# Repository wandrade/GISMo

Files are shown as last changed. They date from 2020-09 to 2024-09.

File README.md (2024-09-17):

# G.I.S.Mo

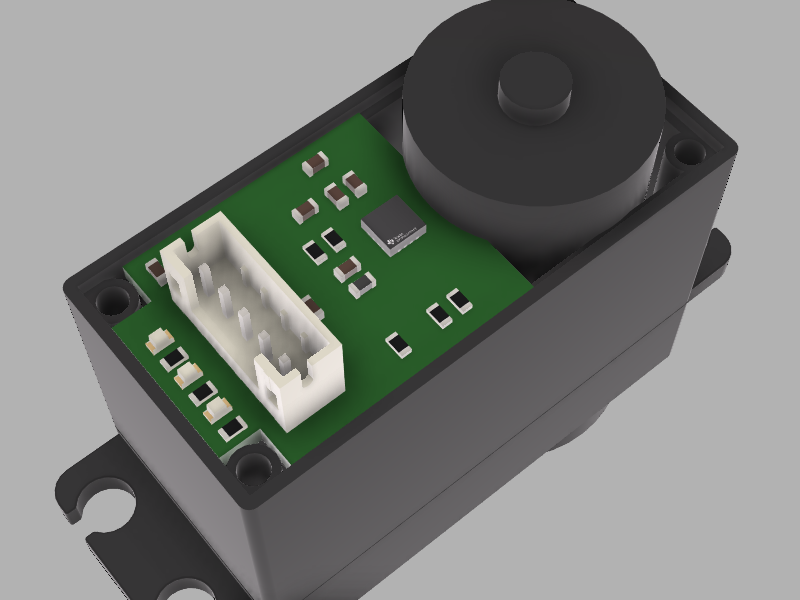
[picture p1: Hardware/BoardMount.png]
Board Mount
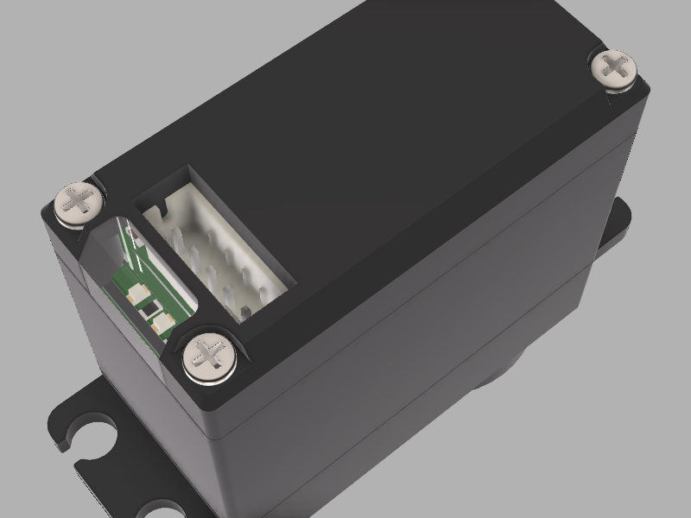
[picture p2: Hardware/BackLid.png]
G.I.S.Mo Board
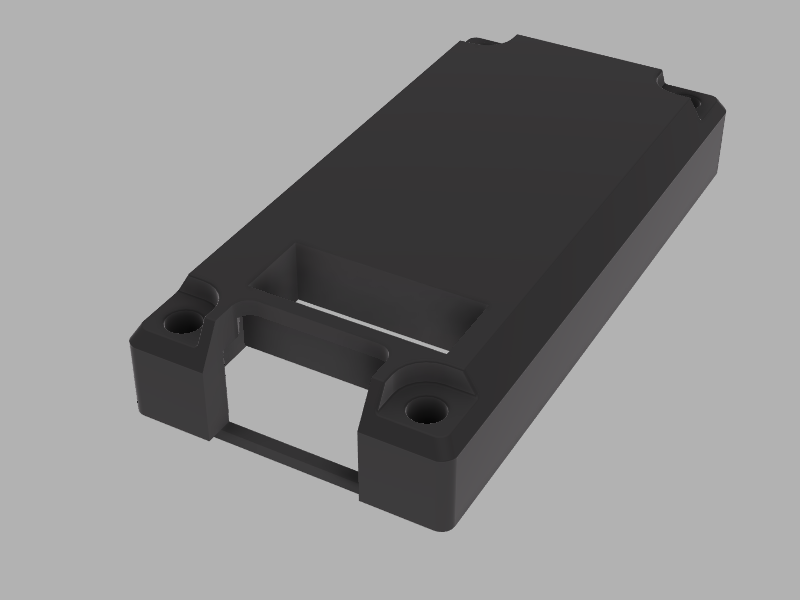
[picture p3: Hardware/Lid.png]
Lid
  |   | 
:-------------------------:|:-------------------------:|:-------------------------:

After a long search, I have failed to find a servo motor that does everything I need for my projects that is also cheap(ish) and fully programmable (say no to closed source stuff whenever you can).

Well, thus was born the idea of GISMo (Greatly Inteligent Servo Motor). This project aims to develop a board that can be used to replace the vanilla servo driver boards that comes with cheaper ones such as MG995 and MG996R, giving it more power and making it more usefull for distributed controll projects:

Wishlist:
- [x] Embedded MCU (STM32F302 powered!) 
- [x] Current sensing (for torque controll and power management features) 
- [ ] I2C interface (or if you please, just change a bit the circuit to use whatever interface you want)
- [x] Programable LED's (because they are cool)
- [x] Absolute magnetic encoder (at least 12bits)
- [x] Free range of movement (180 degrees is just not enough)
- [ ] Control:
    - [ ] Simple position PID loop
    - [ ] MISO controller for speed and position simultaniously (Probably a state space controller)
    - [ ] Torque controll loop
    - [ ] Trapezoidal position curve following
- [ ] Configurable parameters
    - [ ] Speed/Position/Current limit
    - [ ] Controller mode
    - [ ] Configurable break zone (turn on break when position reaches its demand and settles)
    - [ ] Multiturn counter
    - [ ] Controller gains (PID and state space gain matrix)
- [ ] ROS2 Interface node:
    - [ ] Hot plug I2C device detection
    - [ ] Configuration via YAML and ROS Param
    - [ ] up to 16 Individually addressed servos

# Organization
The project contains 3 main blocks: first is the hardware, using [KiCad](https://kicad-pcb.org/), in the Hardware folder you will find 2 subfolders, one for the dev board, which is a big version of the board with some more stuff to facilitate firmware development and debugging, and a second one that contains the GISMo board that actually fits in the servo (to be made).
Then we have the Firmware with two other bits, the [CubeMX](https://www.st.com/en/development-tools/stm32cubemx.html) project so we have everything neatly initialized in our MCU, and the actual firmware and its libs.

# Version History
Now this is a bit tricky. I have 3 things to version and no interest in havving 3 different repos for them at all, so ill trake and make it sensible.

Each sub-thing will have its own sub-version, and once I have a combination of the 3 of them that kind of works, I will merge it into the master branch and tag it with a overall version of the repo (if that makes sense).

## Firmware
--

## GISMo Board
- [Interactive BOM](http://htmlpreview.github.io/?https://github.com/wandrade/GISMo/blob/develop/Hardware/GISMoBoard/bom/ibom.html)

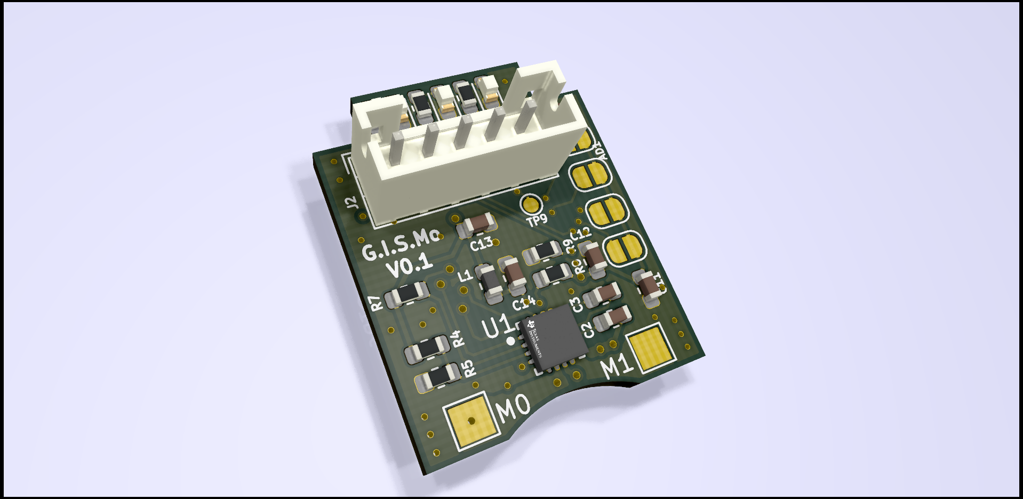
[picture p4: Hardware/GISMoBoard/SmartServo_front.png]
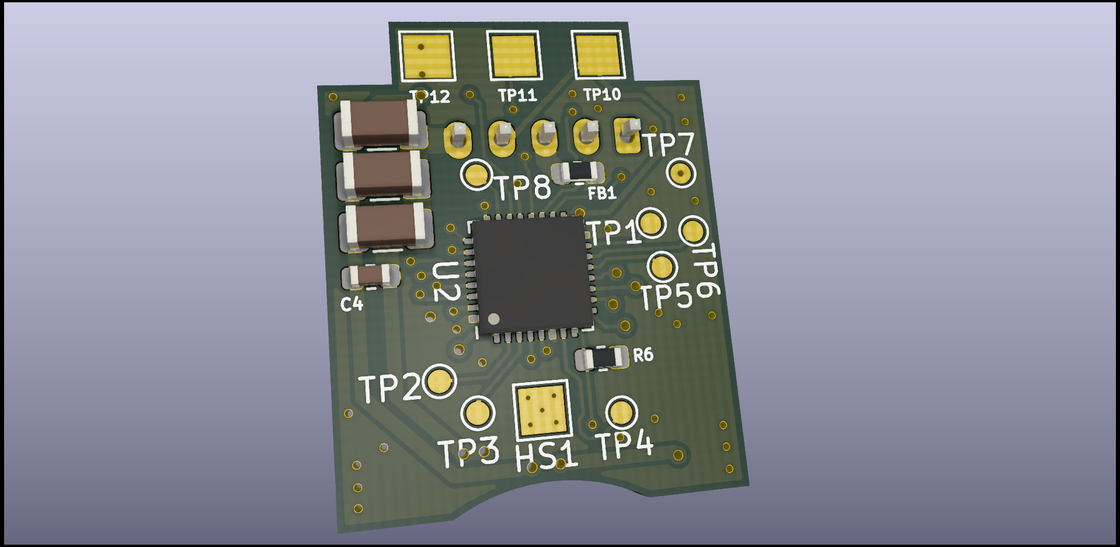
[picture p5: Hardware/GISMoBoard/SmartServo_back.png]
 | 
:-------------------------:|:-------------------------:
- 0.0.1 - Copy of dev board with a few changes to reduce space usage
    - Only one I2C/Power plug
    - Replaced Address header pins by solder jumpers
    - Motor and PWM sensor connectors replaced with solder pads
    - Included a heat sink pad under the motor driver
    - Removed Crystal and oscilator
    - Reduced LED packages
    - Removed Debug connector
    - Removed reset button

## Development Board
- [Interactive BOM](http://htmlpreview.github.io/?https://github.com/wandrade/GISMo/blob/develop/Hardware/DevBoard/bom/ibom.html)

This board is meant for circuit testing and ease of debugging.
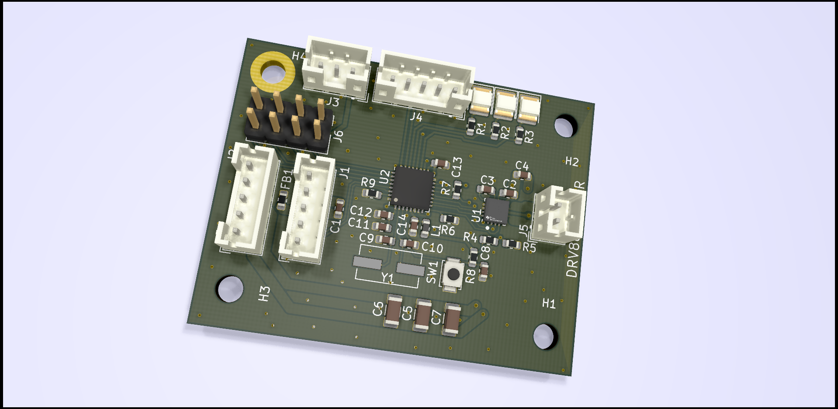
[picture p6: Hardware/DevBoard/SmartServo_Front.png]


- 0.0.1 - Initial proposal board for development board schematic and layout.
    - [STM32F302K8 MCU](https://www.st.com/en/microcontrollers-microprocessors/stm32f302k8.html) - Small package and seemingly enough processing power for everything we need.
    - [DRV8876RGTR Driver](https://www.ti.com/store/ti/en/p/product/?p=DRV8876RGTR) - Has more than double the current needed and provides an inbuilt current sensing solution (hopefully good enough)

# Costs
Here I will keep track of how much you have to pay for each of the more expensive bits so you have an idea of how much a working GISMo will cost you.

# FAQ
I have barely started this project and everytime I tell somebody about it, I get the same questions, so here we go:

- Why not use a normal DC motor with drivers tailored for each project:
    - Cause I like modular! It saves time and you dont have to do everything multiple times. Plus, a lot of the stuf you find online if you are 3D printing, is already made for this size motor. Plus Plus, sorting out motor specifications, gearboxes, making gears (when necessary) is all just a pain, this one can do a lot of the stuff I need for anyway (robotic arms and legged robots).

- Why not just buy a smart servo? this one will probably cost almost the same as the comercial ones.
    - For one, i Hope to make it at least the same price as the "cheap" smart servos. But really, mainly, so I can have full power over its features and its firmware. Also cause its fun!

For now that is it, lets see what comes next :)

# License
Everything under this repository is free to use unless it is used to generate profit. The license states that it CAN be used for comercial puproses, however an agreement have to be reached between the original creator of this project (Werner Thomassen Andrade) and the interested parties before that can happens.

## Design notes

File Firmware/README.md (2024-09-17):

# G.I.S.Mo Firmware

This section of the repo is all about the firmware powering the board. Architecture, implementation decisions, methods and so on.

# Overall Structure
The firmware has a few main components:
- PWM position encoder reading
- Motor current reading
- Control algorithms
- Communications and interface

Each one will be detailed as they are developed
## Softwares and tools
CubeMX
CubeMonitor
CubeIDE

## I²C interface
To learn more about it and how to implemente it go to these articles:
* https://deepbluembedded.com/stm32-i2c-tutorial-hal-examples-slave-dma/
* https://visualgdb.com/tutorials/arm/stm32/i2c/

and have a look. It is very easy and well explained, starting from the theory then jumpping into the implementation used by STM32 MCUs

## PWM Encoder
### Choosing an encoder
This projects aims to use either the magnetic encoder [AS5600](https://www.mouser.co.uk/datasheet/2/588/AS5600_DS000365_5-00-1877365.pdf) or [AS5048x](https://ams.com/documents/20143/36005/AS5048_DS000298_4-00.pdf/910aef1f-6cd3-cbda-9d09-41f152104832). They both have the same PWM interface so it should be just a matter of choosing your preference and it will work.

They are part of a [family of magnetic absolute encoders](https://ams.com/angle-position-on-axis) that can read the orientation of a magnet with respect to the chip with high precision and speed.
The chips are robust to external magnetic fields, temperature changes and slight mechanical variations such as eccentricity and distance from the chip, making it a very robust and easy to use option. The downside? Cost, mor on that soon.

So I reckon that 12bits (that is down to 0.08789 degrees)it more than enough in terms of precision for a smart servo and the purposes that we are aiming for here, there are cheaper versions of such encoders that have a smaller precision such as 10bits but that is just not enough. of course if 14 and 16 and 22 bit would be awesome... but not so much when we have every intention of making at least 12 of these motors to build a nice robot spider.  So on that range there are a few choices as you can see in the links above, but two of them caught my attention and here is why:

- AS5600 - One of the cheapest ones, goes for around £2.50 a pop. downside is that you have to pre-configure the PWM output to run at a high frequency, and it only get to 920Hz.
- AS5048x - 3 Times the price of the above, but its slightly faster (1Khz) and come ready t go, you just solder it to the PCB and plug it in.

Arguably that is not fast enough for a position encoder, especially since we are deriving the speed out of it too. But for most applications that should be enough. If not then hey! this is open source! feel free to slightly change the pins you expose for the sensor and you can use something faster or with better precision such as the AS5048 SSI interface or any other encoder that suits you really.

### Reading it
While explaining how i have implemented the sensor reading, I assume you have the code open on the other half of the screen so you can actually know what im talking about.

Now on the datasheet there is a nice diagram of the PWM signal that you can expect out of the chip (just click on the link of the previous section of any of the encoders and search for 'PWM' you will find it in no time).

For reading a PWM without risking to loose any valuable readings due to bad implementation (and after much trial and error), I have found that the best way is to get a timer on the pin that has both direct and indirect capture on separate channels (Just open the CubeMX project and look at how timer 1 is configured).

This will allow me to start 2 interrupts on the same pin, one for the rising edge of the PWM and another for the falling edge.
As stated in the datasheet, the signal is not 100% information, you have in total 4119 clocks on each cycle, 12 are always high as a 'init' bit set, then there are 4 reserved for errors, then the next 4095 are the actual data and finally some more 8 clocks that are always low, as e 'exit' bit set.

The full duty cycle can vary a little bit, so its better to also read the period of each one to use in the calculations so we have a more precise measure. Right to continuing...

You set an interrupt at the falling edge (after the duty cycle is completed) but you don't need to set up a callback function for it. All we need to know is when that edge ocurred, and we don't need to waste CPU time putting that into a variable, since the chip already does that for us, we just have to access it like 'htim1.Instance.CCR#' where # is the number of the channel that got interrupted.

On the rising edge tho, we want to have a callback, but it has to be really fast (otherwise we wont have enough CPU for al the rest), in order to spent less CPU time on bullshit, I have disabled the code generation for timer1 (On cubeMX System Core->NVIC->Tim1 capture compare interrupt) because the HAL implementation of it that all tutorials tell you to use do LOADS of ifs and elses to check what sort of interrupt that is and that is just a waste of time, since we know what timer 1 is being used for. After disabling the code generation, all we have to do is define the 'void TIM1_CC_IRQHandler(void)' function on the main and that is our callback, simple as that. (look at the code for the other stuff you have to do in there).

Now that the callback is handled, what we need to do to fully read our position goes as follow (and you can see the full implementation just by following everything in void TIM1_CC_IRQHandler(void) on main.c):

- Reset timer - We want the timer count to start at the beginning of the cycle, and then finish at the end of it (obviously) and that will be your full period time.
- Save CCR3 and CCR4 (interupt times of rising and falling edges) ASAP - They get overwritten when another interrupt comes in, so we want to save that into another variable to be able to use it reliably all the way trough.
- Transform the timer count of our CPU (which is running at 64Mhz, so around 64K counts per period) to the clock timing of the sensor, which is 4119 per cycle.
- Process the data
    - Some error checking is always good (if there is not enough clock times that means that there is an error on the sensor, if there is too much it means there is no sensor at all).
    - Calculate the position of the encoder
    - (Optional) Count the number of turns that happened for multiturn applications.
    - Put both single turn position and multiturn count in one variable. why?
        - After the callback finishes, we need to read those values on lower priority threads to actually use it, so you want to be sure that you have read the whole thing before starting to process. If you have to read two variables, you might get interrupted after reading the first one, then another measures come in and then you read the second one of a different reading, so you get inconsistent data.
        - If you put them together like i did there, you have just one number that tells you the absolute position including multiturn, it just works nicely, and you only have to scale the thing once to transform from raw to readable angle.
- That is it!

The thread that does this will have the highest priority of the bunch for reasons that will be explained in the section appropriate for that. (You can set this priority on CubeMx under System Core->NVIC->Tim1 capture compare interrupt).

Maybe i'll put some diagrams and pictures here in the future to make this easier to understand, who knows?!

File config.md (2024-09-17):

sudo tar xjf gcc-arm-none-eabi-YOUR-VERSION.bz2 -C /usr/share/

sudo ln -s /usr/share/gcc-arm-none-eabi-YOUR-VERSION/bin/arm-none-eabi-gcc /usr/local/bin/arm-none-eabi-gcc 
sudo ln -s /usr/share/gcc-arm-none-eabi-YOUR-VERSION/bin/arm-none-eabi-g++ /usr/local/bin/arm-none-eabi-g++
sudo ln -s /usr/share/gcc-arm-none-eabi-YOUR-VERSION/bin/arm-none-eabi-gdb /usr/local/bin/arm-none-eabi-gdb
sudo ln -s /usr/share/gcc-arm-none-eabi-YOUR-VERSION/bin/arm-none-eabi-size /usr/local/bin/arm-none-eabi-size
sudo ln -s /usr/share/gcc-arm-none-eabi-YOUR-VERSION/bin/arm-none-eabi-objcopy /usr/local/bin/arm-none-eabi-objcopy

sudo apt install libncurses-dev
sudo ln -s /usr/lib/x86_64-linux-gnu/libncurses.so.6 /usr/lib/x86_64-linux-gnu/libncurses.so.5
sudo ln -s /usr/lib/x86_64-linux-gnu/libtinfo.so.6 /usr/lib/x86_64-linux-gnu/libtinfo.so.5

install USBIP Connect vscode extention in wsl
install the client on windows host
(follow instructions on extention page)

sudo apt install openocd

install extension VsCode Action Buttons

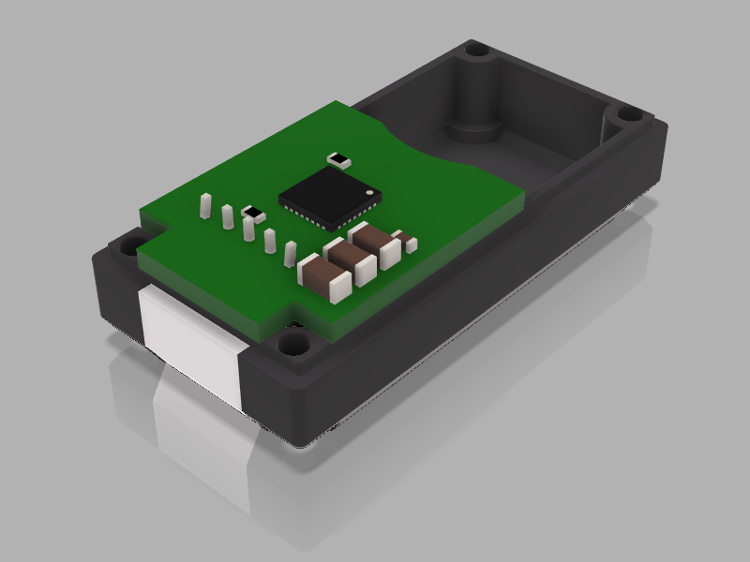
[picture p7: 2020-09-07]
Hardware/Lid_with_PCB.png

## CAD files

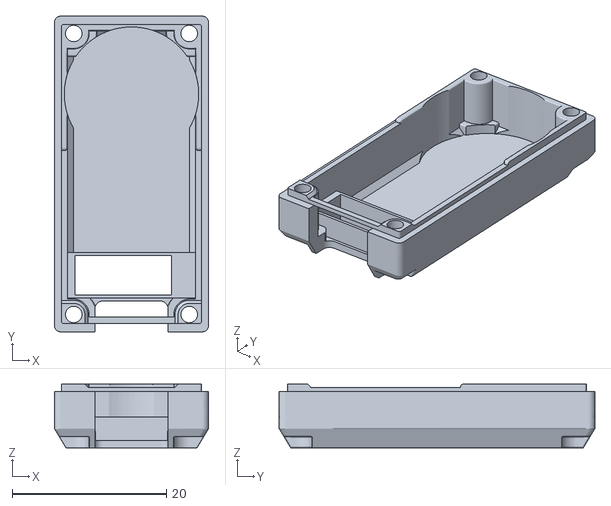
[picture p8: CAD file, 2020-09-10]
Hardware/BackLid.stl
20.0 x 41.0 x 8.30

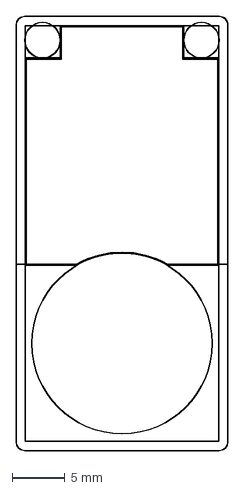
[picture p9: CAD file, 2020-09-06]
Hardware/GISMoBoard/BoardOutline.dxf
20.0 x 41.0 mm

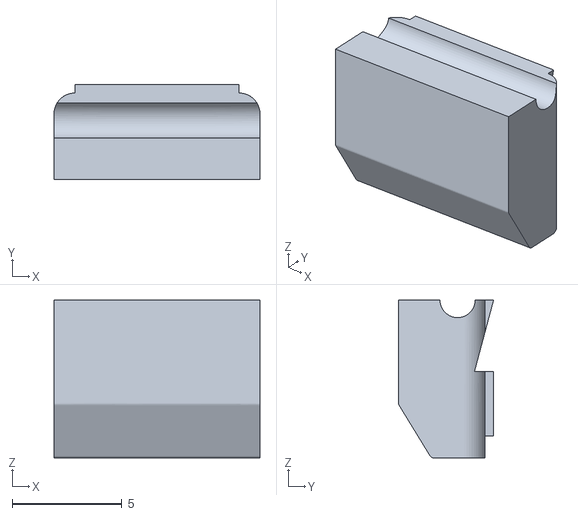
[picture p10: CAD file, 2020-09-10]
Hardware/LED_Screen.stl
9.40 x 4.34 x 7.20

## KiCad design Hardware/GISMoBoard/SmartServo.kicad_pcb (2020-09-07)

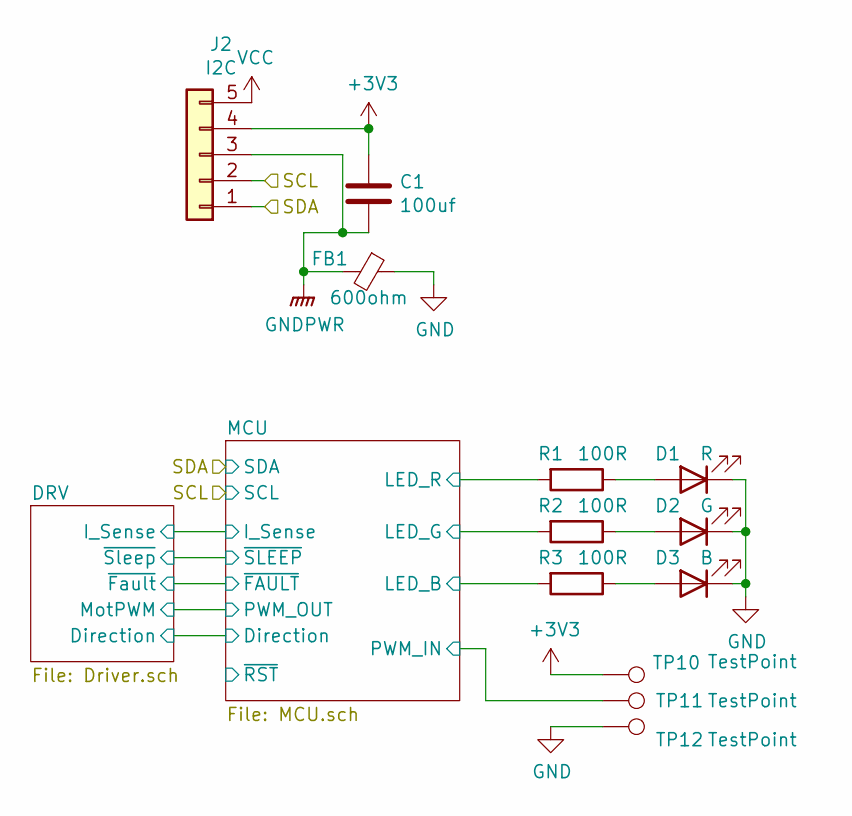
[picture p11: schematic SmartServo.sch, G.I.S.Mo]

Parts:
C1: 100uf; C_0603_1608Metric
D1: R; LED_0603_1608Metric
D2: G; LED_0603_1608Metric
D3: B; LED_0603_1608Metric
FB1: 600ohm; R_0603_1608Metric
J2: I2C; JST_PH_B5B-PH-K_1x05_P2.00mm_Vertical
R1, R2, R3: 100R; R_0603_1608Metric
TP10, TP11, TP12: TestPoint; TestPoint_Pad_2.0x2.0mm

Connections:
+3V3: C1.1, J2.4, TP10.1; also elsewhere on the board
/MCU/LED_B: R3.2; also elsewhere on the board
/MCU/LED_G: R2.2; also elsewhere on the board
/MCU/LED_R: R1.2; also elsewhere on the board
/MCU/PWM_IN: TP11.1; also elsewhere on the board
/SCL: J2.2; also elsewhere on the board
/SDA: J2.1; also elsewhere on the board
GND: D1.1 (K), D2.1 (K), D3.1 (K), FB1.1, TP12.1; also elsewhere on the board
GNDPWR: C1.2, FB1.2, J2.3; also elsewhere on the board
unnamed: D1.2 (A), R1.1
unnamed: D2.2 (A), R2.1
unnamed: D3.2 (A), R3.1
VCC: J2.5; also elsewhere on the board

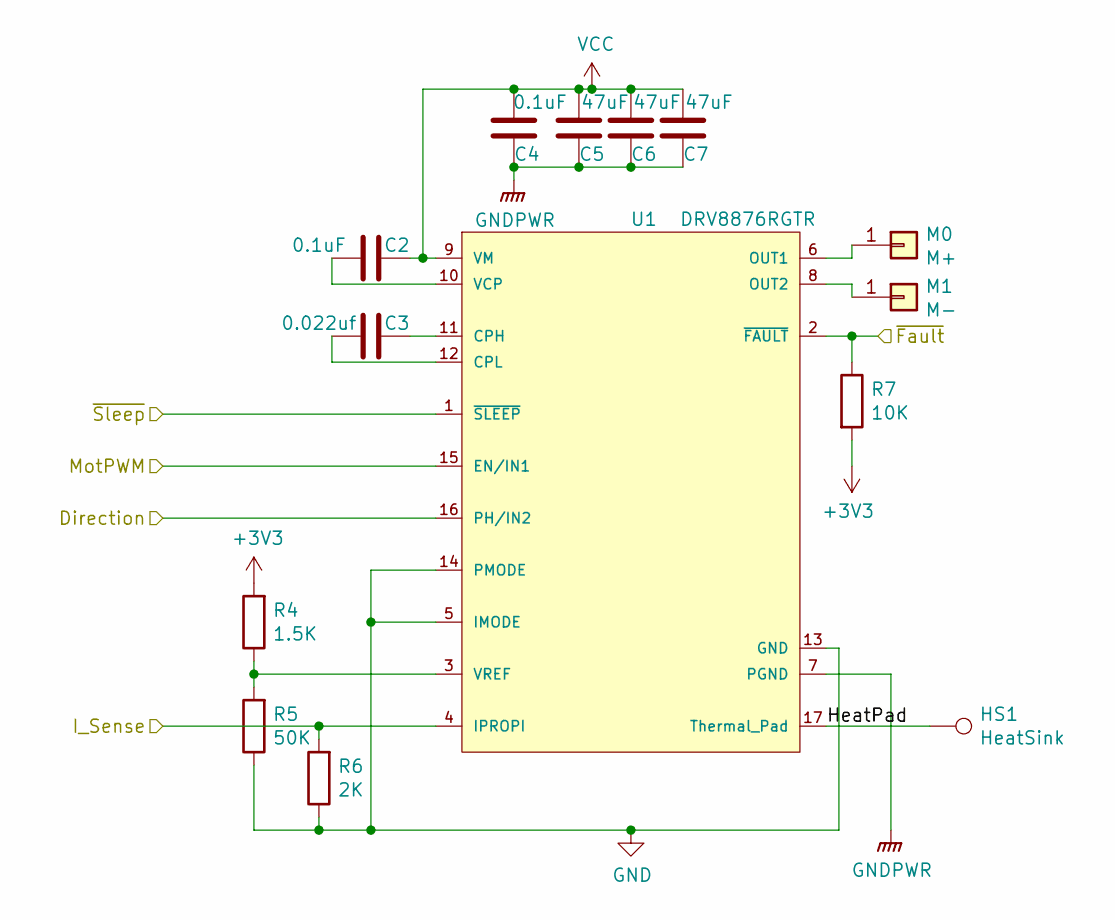
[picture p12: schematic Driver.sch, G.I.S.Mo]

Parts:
C2, C4: 0.1uF; C_0603_1608Metric
C3: 0.022uf; C_0603_1608Metric
C5, C6, C7: 47uF; C_1206_3216Metric; Farnell https://uk.farnell.com/tdk/c3216x5r1e47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
HS1: HeatSink; TestPoint_Pad_2.0x2.0mm
M0: M+; TestPoint_Pad_2.0x2.0mm
M1: M-; TestPoint_Pad_2.0x2.0mm
R4: 1.5K; R_0603_1608Metric
R5: 50K; R_0603_1608Metric
R6: 2K; R_0603_1608Metric
R7: 10K; R_0603_1608Metric
U1: DRV8876RGTR; Texas_Instruments-RGT0016C-0-0-MFG; mouser part number 595-DRV8876RGTR

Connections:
+3V3: R4.2, R7.2; also elsewhere on the board
/DRV/Direction: U1.16 (PH/IN2); also elsewhere on the board
/DRV/HeatPad: HS1.1, U1.17 (Thermal_Pad)
/DRV/I_Sense: R6.2, U1.4 (IPROPI); also elsewhere on the board
/DRV/MotPWM: U1.15 (EN/IN1); also elsewhere on the board
/MCU/~FAULT: R7.1, U1.2 (~FAULT~); also elsewhere on the board
/MCU/~SLEEP: U1.1 (~SLEEP~); also elsewhere on the board
GND: R5.1, R6.1, U1.5 (IMODE), U1.13 (GND), U1.14 (PMODE); also elsewhere on the board
GNDPWR: C4.1, C5.1, C6.1, C7.1, U1.7 (PGND); also elsewhere on the board
unnamed: C2.2, U1.10 (VCP)
unnamed: C3.1, U1.11 (CPH)
unnamed: C3.2, U1.12 (CPL)
unnamed: M0.1, U1.6 (OUT1)
unnamed: M1.1, U1.8 (OUT2)
unnamed: R4.1, R5.2, U1.3 (VREF)
VCC: C2.1, C4.2, C5.2, C6.2, C7.2, U1.9 (VM); also elsewhere on the board

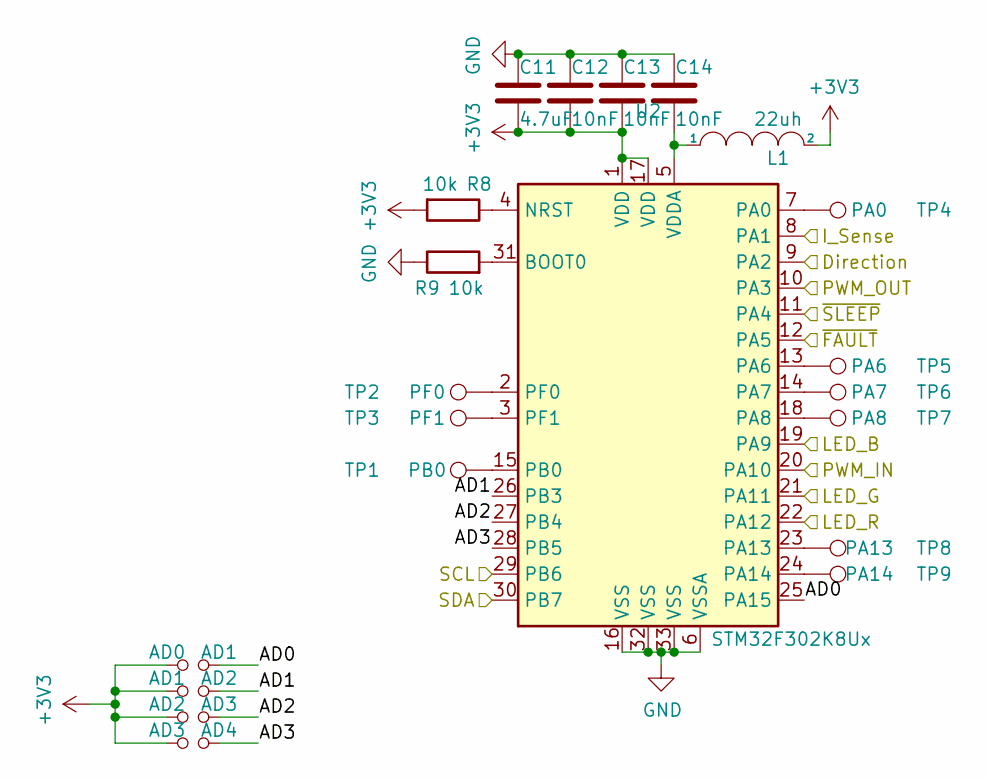
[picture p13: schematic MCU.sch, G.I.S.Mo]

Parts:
AD1: AD0; SolderJumper-2_P1.3mm_Open_RoundedPad1.0x1.5mm
AD2: AD1; SolderJumper-2_P1.3mm_Open_RoundedPad1.0x1.5mm
AD3: AD2; SolderJumper-2_P1.3mm_Open_RoundedPad1.0x1.5mm
AD4: AD3; SolderJumper-2_P1.3mm_Open_RoundedPad1.0x1.5mm
C11: 4.7uF; C_0603_1608Metric
C12, C13, C14: 10nF; C_0603_1608Metric
L1: 22uh; L_0603_1608Metric
R8, R9: 10k; R_0603_1608Metric
TP1: PB0; TestPoint_Pad_D1.0mm
TP2: PF0; TestPoint_Pad_D1.0mm
TP3: PF1; TestPoint_Pad_D1.0mm
TP4: PA0; TestPoint_Pad_D1.0mm
TP5: PA6; TestPoint_Pad_D1.0mm
TP6: PA7; TestPoint_Pad_D1.0mm
TP7: PA8; TestPoint_Pad_D1.0mm
TP8: PA13; TestPoint_Pad_D1.0mm
TP9: PA14; TestPoint_Pad_D1.0mm
U2: STM32F302K8Ux; QFN-32-1EP_5x5mm_P0.5mm_EP3.45x3.45mm

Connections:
+3V3: AD1.1, AD2.1, AD3.1, AD4.1, C11.2, C12.2, C13.2, L1.2, R8.2, U2.1 (VDD), U2.17 (VDD); also elsewhere on the board
/DRV/Direction: U2.9 (PA2); also elsewhere on the board
/DRV/I_Sense: U2.8 (PA1); also elsewhere on the board
/DRV/MotPWM: U2.10 (PA3); also elsewhere on the board
/MCU/AD0: AD1.2, U2.25 (PA15)
/MCU/AD1: AD2.2, U2.26 (PB3)
/MCU/AD2: AD3.2, U2.27 (PB4)
/MCU/AD3: AD4.2, U2.28 (PB5)
/MCU/LED_B: U2.19 (PA9); also elsewhere on the board
/MCU/LED_G: U2.21 (PA11); also elsewhere on the board
/MCU/LED_R: U2.22 (PA12); also elsewhere on the board
/MCU/PWM_IN: U2.20 (PA10); also elsewhere on the board
/MCU/~FAULT: U2.12 (PA5); also elsewhere on the board
/MCU/~SLEEP: U2.11 (PA4); also elsewhere on the board
/SCL: U2.29 (PB6); also elsewhere on the board
/SDA: U2.30 (PB7); also elsewhere on the board
GND: C11.1, C12.1, C13.1, C14.1, R9.1, U2.6 (VSSA), U2.16 (VSS), U2.32 (VSS), U2.33 (VSS); also elsewhere on the board
unnamed: C14.2, L1.1, U2.5 (VDDA)
unnamed: R8.1, U2.4 (NRST)
unnamed: R9.2, U2.31 (BOOT0)
unnamed: TP1.1, U2.15 (PB0)
unnamed: TP2.1, U2.2 (PF0)
unnamed: TP3.1, U2.3 (PF1)
unnamed: TP4.1, U2.7 (PA0)
unnamed: TP5.1, U2.13 (PA6)
unnamed: TP6.1, U2.14 (PA7)
unnamed: TP7.1, U2.18 (PA8)
unnamed: TP8.1, U2.23 (PA13)
unnamed: TP9.1, U2.24 (PA14)

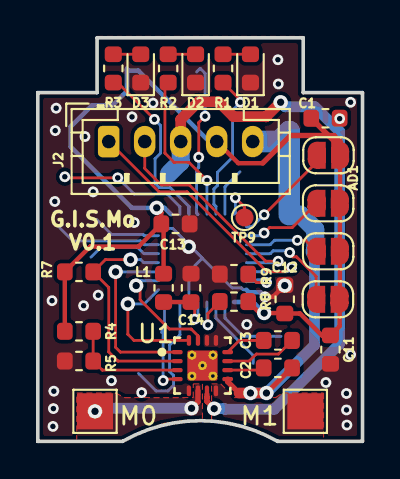
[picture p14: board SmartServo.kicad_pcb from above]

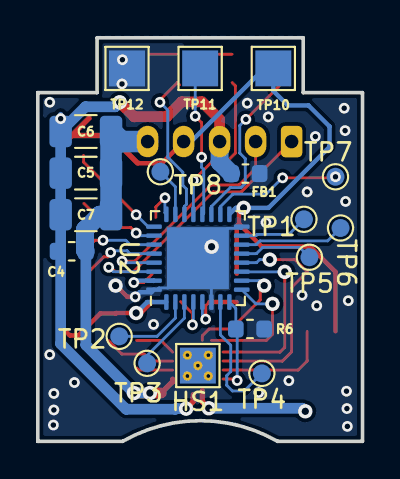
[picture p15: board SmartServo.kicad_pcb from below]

Board: 2 copper layers, 18.0 x 22.4 mm, 47 parts (19 on the bottom side), 41 nets.

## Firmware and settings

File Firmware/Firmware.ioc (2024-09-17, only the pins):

Mcu.UserName=STM32F302K8Ux
PA0.GPIO_Label=DEBUG_1
PA0.Signal=GPIO_Output
PA1.GPIO_Label=I_Sense
PA1.Signal=ADC1_IN2
PA10.GPIO_Label=PWM_IN
PA10.Signal=S_TIM1_CH3
PA11.GPIO_Label=LED_G
PA11.Signal=GPIO_Output
PA12.GPIO_Label=LED_R
PA12.Signal=GPIO_Output
PA13.Signal=SYS_JTMS-SWDIO
PA14.Signal=SYS_JTCK-SWCLK
PA15.GPIO_Label=AD0
PA15.Signal=GPIO_Input
PA2.GPIO_Label=Direction
PA2.Signal=GPIO_Output
PA3.GPIO_Label=PWM_Out
PA3.Signal=S_TIM2_CH4
PA4.GPIO_Label=nSleep
PA4.Signal=GPIO_Output
PA5.GPIO_Label=nFault
PA5.Signal=GPIO_Input
PA6.GPIO_Label=DEBUG_2
PA6.Signal=GPIO_Output
PA7.GPIO_Label=DEBUG_3
PA7.Signal=GPIO_Output
PA8.GPIO_Label=DEBUG_5
PA8.Signal=GPIO_Output
PA9.GPIO_Label=LED_B
PA9.Signal=GPIO_Output
PB0.GPIO_Label=DEBUG_4
PB0.Signal=GPIO_Output
PB3.GPIO_Label=AD1
PB3.Signal=GPIO_Input
PB4.GPIO_Label=AD2
PB4.Signal=GPIO_Input
PB5.GPIO_Label=AD3
PB5.Signal=GPIO_Input
PB6.Signal=I2C1_SCL
PB7.Signal=I2C1_SDA

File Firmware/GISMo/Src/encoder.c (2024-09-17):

#include "encoder.h"

ENCODER_STRUCT encoder;
extern TIM_HandleTypeDef htim1;
extern data_register_t data_register;

void init_encoder(){
	  HAL_TIM_IC_Start_IT(&htim1, TIM_CHANNEL_3); // Rising edge
	  HAL_TIM_IC_Start(&htim1, TIM_CHANNEL_4); // Falling Edge - Initialise interrupt capture but no callback function (We only need the CCR4 value)
}

// Define interrupt function
void TIM1_CC_IRQHandler(void)
{
	// Check if it comes from channel3
	if(__HAL_TIM_GET_IT_SOURCE(&htim1, TIM_IT_CC3) != RESET){
		// Clear interrupt flag on channel 3
		__HAL_TIM_CLEAR_IT(&htim1, TIM_IT_CC3);
		// Set counter to 65 which is how long it takes for this function to zero (to its like setting it to zero as soon as the PWM sensor rising edge is detected) with a bit of tweaking
		// until i got some known values (e.g. 12 when no magnet is close to the encoder)
		// This value was obtained experimentally by measuring the number of CPU clocks it took to run all these functions (https://www.embedded-computing.com/articles/measuring-code-execution-time-on-arm-cortex-m-mcus)
		__HAL_TIM_SET_COUNTER(&htim1, 65);
		update_encoder(&htim1);
	}
}

void update_encoder(TIM_HandleTypeDef* htim){
	// Reset timer ASAP so we can consider 0 as the start of the period,
	// falling edge time as the end of duty cycle and rising time (from next cycle) as the total period time
	encoder.t_rising_edge = htim->Instance->CCR3;
	encoder.t_falling_edge = htim->Instance->CCR4;

	// Get number of clocks of the encoder (4119 per full cycle)
	encoder.pwm_clocks = encoder.t_falling_edge*ENCODER_CLOCKS_PER_CYCLE/encoder.t_rising_edge;


	if(encoder.pwm_clocks >= ENCODER_MIN_VALID_CLOCK_NUM && encoder.pwm_clocks <= ENCODER_MAX_VALID_CLOCK_NUM){
		// Reset error flag
		encoder.error = 0;

		// Calculate singleturn
		encoder.single_prev = encoder.single;
		encoder.single = encoder.pwm_clocks - ENCODER_MIN_VALID_CLOCK_NUM;

		// Multiturn count
		if(encoder.single_prev > 3000 && encoder.single < 1000) // also considers if last measure wasn't an error
			encoder.multiturn_counter++; // positive turn - singleturn goes from a big number to a very small one
		else if (encoder.single_prev < 1000 && encoder.single > 3000) // also considers if last measure wasn't an error
			encoder.multiturn_counter--; // negative turn - singleturn goes from a small number to a very big one

		// Concatenate singleturn and multiturn counters
		encoder.raw = (encoder.multiturn_counter << 12) | encoder.single;
		data_register.s.encoder_raw = encoder.raw;
		data_register.s.encoder_multiturn = encoder.multiturn_counter;

	} else {
		encoder.error++; // Counts consecutive errors;
		if(!encoder.error) encoder.error++; // If overflows, make sure it goes from 0 to 1 again
		data_register.s.encoder_error = encoder.error;
	}

}


//extern POSITION_STRUCT position;
//extern SPEED_STRUCT speed;


// Get period in seconds
//	encoder.period = (float)encoder.t_rising_edge/(float)TIMER_FREQUENCY;

//void initialize_encoder(){
//	position.filter_size = 5;		// How many readings are averaged for the filtered position reading
//	position.spike_limit = 0.1;		// Max allowed position variation (bigger than this will be discarded)
//	position.spike_counter = 5;		// How many spikes in a row can the system accept before ignoring the spike filter
//}
//
//void update_position_raw(TIM_HandleTypeDef* htim){
//	// Reset timer counter for next interrupt pair
//	__HAL_TIM_SET_COUNTER(htim, 0);
//	position.CCR3 = htim->Instance->CCR3; 	// Rising edge time (channel 3 interrupt time)
//	position.CCR4 = htim->Instance->CCR4; 	// Falling edge time (channel 4 interrupt time)
//
//	// Falling this might happen when position is close to 360 degrees and there is not enough time to process interrupt
//	if(position.CCR4 >= position.CCR3 && position.CCR4 - position.CCR3 < 64000){
//		// Calculate PWM duty cycle
//		position.raw = position.CCR4 - position.CCR3;
//		// Convert Duty cycle into useful stuff
//		update_position_speed();
//	}
//
//}
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

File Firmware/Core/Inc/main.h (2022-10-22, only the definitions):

#define DEBUG_1_Pin GPIO_PIN_0
#define DEBUG_1_GPIO_Port GPIOA
#define I_Sense_Pin GPIO_PIN_1
#define I_Sense_GPIO_Port GPIOA
#define Direction_Pin GPIO_PIN_2
#define Direction_GPIO_Port GPIOA
#define PWM_Out_Pin GPIO_PIN_3
#define PWM_Out_GPIO_Port GPIOA
#define nSleep_Pin GPIO_PIN_4
#define nSleep_GPIO_Port GPIOA
#define nFault_Pin GPIO_PIN_5
#define nFault_GPIO_Port GPIOA
#define DEBUG_2_Pin GPIO_PIN_6
#define DEBUG_2_GPIO_Port GPIOA
#define DEBUG_3_Pin GPIO_PIN_7
#define DEBUG_3_GPIO_Port GPIOA
#define DEBUG_4_Pin GPIO_PIN_0
#define DEBUG_4_GPIO_Port GPIOB
#define DEBUG_5_Pin GPIO_PIN_8
#define DEBUG_5_GPIO_Port GPIOA
#define LED_B_Pin GPIO_PIN_9
#define LED_B_GPIO_Port GPIOA
#define PWM_IN_Pin GPIO_PIN_10
#define PWM_IN_GPIO_Port GPIOA
#define LED_G_Pin GPIO_PIN_11
#define LED_G_GPIO_Port GPIOA
#define LED_R_Pin GPIO_PIN_12
#define LED_R_GPIO_Port GPIOA
#define AD0_Pin GPIO_PIN_15
#define AD0_GPIO_Port GPIOA
#define AD1_Pin GPIO_PIN_3
#define AD1_GPIO_Port GPIOB
#define AD2_Pin GPIO_PIN_4
#define AD2_GPIO_Port GPIOB
#define AD3_Pin GPIO_PIN_5
#define AD3_GPIO_Port GPIOB

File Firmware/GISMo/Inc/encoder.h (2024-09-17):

// encoder.h
#ifndef ENCODER_H
#define ENCODER_H

#define TIMER_FREQUENCY				64000000	// in Hz (timer 1 is on APB2 according to datasheet)
#define ENCODER_CLOCKS_PER_CYCLE	4119		// see datasheet  (https://ams.com/documents/20143/36005/AS5048_DS000298_4-00.pdf page 27)
#define ENCODER_MAX_VALID_CLOCK_NUM	4111		// The last 8 clocks are always 0 if the sensor is connected and there is a magnet close to it
#define ENCODER_MIN_VALID_CLOCK_NUM	16			// When there is no error, the sensor outputs 16 clocks high at the beggining (12 for init and 4 bit for error code)

#include "stm32f3xx_hal.h"
#include "helper_functions.h"
#include "data.h"
#include <math.h>

typedef struct {
	float period;
	uint32_t t_rising_edge, t_falling_edge;
	uint16_t pwm_clocks;
	uint32_t error;
	uint16_t single, single_prev;
	int32_t multiturn_counter;
	int32_t raw;

} ENCODER_STRUCT;
extern ENCODER_STRUCT encoder;


void init_encoder();
void update_encoder(TIM_HandleTypeDef* htim);


//#define ENCODER_REFRESH_RATE		1000		// in Hz
//#define CLOCK_TICKS_PER_PWM_CYCLE 	4111
//#define PWM_TO_RADIANS_SCALE		0.00153399	// Convert from 12bit raw to and angle in radians
//
//typedef struct {
//	uint32_t raw;
//	uint32_t raw_prev;
//	int32_t multiturn_counter;
//	uint32_t CCR3, CCR4;
//	uint8_t valid;
//	float rad, rad_prev;
//	float rad_multiturn, rad_multiturn_prev;
//	float spike_limit;
//	uint8_t spike_counter;
//
//	// Position filter
//	uint8_t filter_size, buffer_head;
//	float rad_filtered, rad_filtered_prev;
//	float buffer[50];
//
//} POSITION_STRUCT;
//POSITION_STRUCT position;
//
//typedef struct{
//	float rad_sec_raw;
//	float rad_sec, rad_sec_prev;
//} SPEED_STRUCT;
//SPEED_STRUCT speed;
//
//void initialize_encoder();
//void update_position_raw(TIM_HandleTypeDef* htim);
//void update_position_speed();
#endif

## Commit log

2020-09-05 Dev board created
    [Driver.sch, MCU.sch, SmartServo.kicad_pcb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]
2020-09-06 G.I.S.Mo Board
    Mini board first release candidate
    [BoardOutline.dxf, Driver.sch, MCU.sch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]
2020-09-06 Added head sink for motor driver
    [Driver.sch, SmartServo.kicad_pcb]
2020-09-07 Interactive BOM
    [SmartServo.kicad_pcb]
2020-09-07 Added renders and backlid model
    [BackLid.stl, LED Screen.stl]
2020-09-10 3D printable backlid with LED and connectors slot
    [BackLid.stl, LED Screen.stl]
2020-09-10 Removed spaces from file names
    [BoardOutline.dxf, Driver.sch, LED_Screen.stl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]
2020-09-12 FW - Blink LED
2020-09-13 Position sensor reading
2020-09-13 FW - Speed estimation
    Its extremely noisy, could improve if period is measured instead of using fixed value
    [encoder.c, encoder.h, main.h]
2020-09-13 FW - Spike filter on multiturn
    WTF is happening? why doenst it work? u.u
2020-09-14 FW - Bug found
    Still not happy with the position reading tho, will work more on that to make it more robust.
    [encoder.c, encoder.h]
2020-09-14 FW - Proper position encoder reading with no unexpected values
2020-09-15 Explanation of the encoder reading stuff
    Also commented out stuff that I will continue implement later on
2020-09-16 FW - Increased encoder interrupt priority above freeRTOS
2020-09-16 Created driver functions files
2020-09-16 FW - PWM output configured
    Also moved encoder interrupt stuff to encoder.c
2020-09-16 FW - Enable/Disable motor function and some other adjustments
2020-09-17 Initial config for ADC
2020-09-20 ADC on timer and DMA
2020-09-27 FW - Software ADC reading
2020-09-27 FW - ADC on timer event out
2020-09-28 FW - 4KHz current reading
2020-09-28 FW - ADC Scalar
2021-10-02 Separated peripherals into files and added I2C slave addressing
2021-10-02 I2C Broadcast ID
2021-10-09 New I2C reference link
2021-10-14 Basic register based I2C protocol
    Only receives/writes to a buffer
2022-09-22 Read register in I2C implemented
    [Firmware Debug (1).cfg]
2022-10-22 Register setup for reading values over I2C
2022-10-22 FW - Included basic OS based LED PWM driver
2022-10-24 FW - I2C works for both read and write
2024-02-01 I2C more generic
2024-02-08 FINALLY settled on I2C schema, previous one was shite
2024-02-08 LED being controlled by I2C
2024-02-08 I2C nostrech
2024-09-14 Basic position PID controller
2024-09-15 Configured Make and vscode in linux
    [Firmware Debug (1).cfg, stlink-v2-1.cfg, stm32f3x.cfg]
2024-09-15 build clean and flash buttons for the project in vscode
2024-09-17 Refactor gitignore and file paths
    [Firmware Debug (1).cfg]
2024-09-17 Improved controler options and exposed ginas to I2C interface

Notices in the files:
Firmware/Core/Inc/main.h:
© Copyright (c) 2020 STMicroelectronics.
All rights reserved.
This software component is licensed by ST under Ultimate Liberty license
